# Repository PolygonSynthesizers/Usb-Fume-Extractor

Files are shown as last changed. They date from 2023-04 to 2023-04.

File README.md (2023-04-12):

# Usb-Fume-Extractor
This is a USB powered (5v) PWM Computer Fan Controller

Please read until the end!

This fume extractor is made with a 120 mm PWM (4pin) 12V PC Fan. 
You can use any 12V PC Fan as long as the power consomption doesn't exceed 500mA over 12V.
It has to be a 12V fan as the power supply is converting 5V USB to 12V. 24V Fans won't work.
I personally use a Noctua NF-F12 industrialPPC-3000 PWM and it can blow air 
along 6 meter of 80mm aluminium duct even at half speed.

You can control the speed of rotation via the potentiometer around 10 to 90% of the fan full speed.
It works with a 556 chip (which is two 555 timers in DIP 14 pins package) which produce a 5V square pulse
with pulse width modulation (it's how fan speed is controlled on a computer).

You can't power this circuit with a computer USB port. It doesn't have enough power. You have to power it with
a USB Power Supply like a Phone Charger for example. It has to be rated for 1 amp over 5V at a minimum. 
Connect the charger to the board via a USB A to USB A cable or a USB A to USB B cable (Printer cable). 
About the length : the shorter is the better.  

Some references :

* U1 is a NE556 in DIP14 package
* The inductor is a 10 uH Fastron 242408 FPS
* U2 is a LM2731 XMF in SOT-23 package
* R1 and R2 are 0805
* CF1 is 0805
* C1 is 1210
* C2 is 1812
* D1 is .5 amps Schottky Rectifier in SOD-123 package
* All through hole resistors are 1/4W
* All through hole capacitors are 5mm pitch film capacitors
* Except for C7 which is a 2mm pitch aluminium electrolytic.
* RV1 is a Alps Alpine RK09K113 10k Linear (Log can also work but control over speed will not be linear).
* SW1 is a 3 pin SPDT switch with 4.7mm pitch between pins. I has to be rated for 1A at least.

For values you can check the BOM under the bom folder. Values are also on the schematics.
All SMDs can be handsoldered. Start with the LM2731XMF.

This project has been made with KiCad 7.01. You may have to install the latest version of KiCad
for this project to work.
I have made some custom footprints for the switch, the inductor and the film capacitors.
They can be found under the Custom Footprints folder.

Gerbers are available for JLCPCB production under the Gerbers folder. 
Please make your own gerbers if you want to use an other PCB Manufacturer.

I'm providing some 3D files that can be modified on Solidworks. STL Files are also provided so you can print
them on your 3D printer. The rear body of the Fan has been made for 80mm duct. 
Feel free to modifiy it at your own conveniance.
It uses standard M4 screws for the body and M3 screws for the PCB holder.
Files can be found under the 3D Files folder. I will provide some 3d files for the base 
and the PCB front cover later. 
Don't be scared to make your own.

PLEASE DON'T TURN ON THE FAN WITHOUT THE 3D PRINTED FRONT AND REAR BODY PART ATTACHED TO IT !
IT CAN CUT OUT YOUR FINGERS VERY EASILY !
I WON'T TAKE ANY RESPONSABILITY FOR ANY DAMAGE, MATERIAL OR PHYSICAL. YOU HAVE BEEN WARNED !

ENJOY !

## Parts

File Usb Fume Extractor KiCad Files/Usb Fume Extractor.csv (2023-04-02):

# | Reference | Qty | Value | Footprint | DNP
1 | C1 | 1 | 2.2u | Capacitor_SMD:C_1210_3225Metric_Pad1.33x2.70mm_HandSolder
2 | C2 | 1 | 4.7u | Capacitor_SMD:C_1812_4532Metric_Pad1.57x3.40mm_HandSolder
3 | C3, C6 | 2 | 100nf | Capacitor_THT:C_Rect_L7.2mm_W2.5mm_P5.00mm_FKS2_FKP2_MKS2_MKP2
4 | C4 | 1 | 4.7n | Capacitor_THT:C_Rect_L7.2mm_W4.5mm_P5.00mm_FKS2_FKP2_MKS2_MKP2
5 | C5 | 1 | 10nF | Capacitor_THT:C_Rect_L7.2mm_W6.5mm_P5.00mm_FKS2_FKP2_MKS2_MKP2
6 | C7 | 1 | 2.2uF | Capacitor_THT:CP_Radial_D5.0mm_P2.00mm
7 | CF1 | 1 | 220p | Capacitor_SMD:C_0805_2012Metric_Pad1.18x1.45mm_HandSolder
8 | D1 | 1 | MBR0520 | Diode_SMD:D_SOD-123
9 | J1 | 1 | USB_B | Connector_USB:USB_B_OST_USB-B1HSxx_Horizontal
10 | J2 | 1 | Molex 2.54mm | Connector_Molex:Molex_KK-254_AE-6410-04A_1x04_P2.54mm_Vertical
11 | J3 | 1 | USB_A | Connector_USB:USB_A_Wuerth_614004134726_Horizontal
12 | JP1 | 1 | Jumper_2_Bridged | Resistor_THT:R_Axial_DIN0207_L6.3mm_D2.5mm_P10.16mm_Horizontal
13 | L1 | 1 | 10uh | Inductor_SMD:L_Fastron_242408_FPS_Handsoldering
14 | R1 | 1 | 130k | Resistor_SMD:R_0805_2012Metric_Pad1.20x1.40mm_HandSolder
15 | R2 | 1 | 15k | Resistor_SMD:R_0805_2012Metric_Pad1.20x1.40mm_HandSolder
16 | R3, R5 | 2 | 200 | Resistor_SMD:R_0805_2012Metric_Pad1.20x1.40mm_HandSolder
17 | R4 | 1 | 1K | Resistor_THT:R_Axial_DIN0207_L6.3mm_D2.5mm_P10.16mm_Horizontal
18 | R6 | 1 | 6K | Resistor_THT:R_Axial_DIN0207_L6.3mm_D2.5mm_P10.16mm_Horizontal
19 | RA1 | 1 | 6.65K | Resistor_THT:R_Axial_DIN0207_L6.3mm_D2.5mm_P10.16mm_Horizontal
20 | RA2 | 1 | 3.09K | Resistor_THT:R_Axial_DIN0207_L6.3mm_D2.5mm_P10.16mm_Horizontal
21 | RB1 | 1 | 150 | Resistor_THT:R_Axial_DIN0207_L6.3mm_D2.5mm_P10.16mm_Horizontal
22 | RV1 | 1 | 10K | Potentiometer_THT:Potentiometer_Alps_RK09K_Single_Vertical
23 | U1 | 1 | NE556 | Package_DIP:DIP-14_W7.62mm_Socket_LongPads
24 | U2 | 1 | LM2731XMF | Package_TO_SOT_SMD:SOT-23-5_HandSoldering

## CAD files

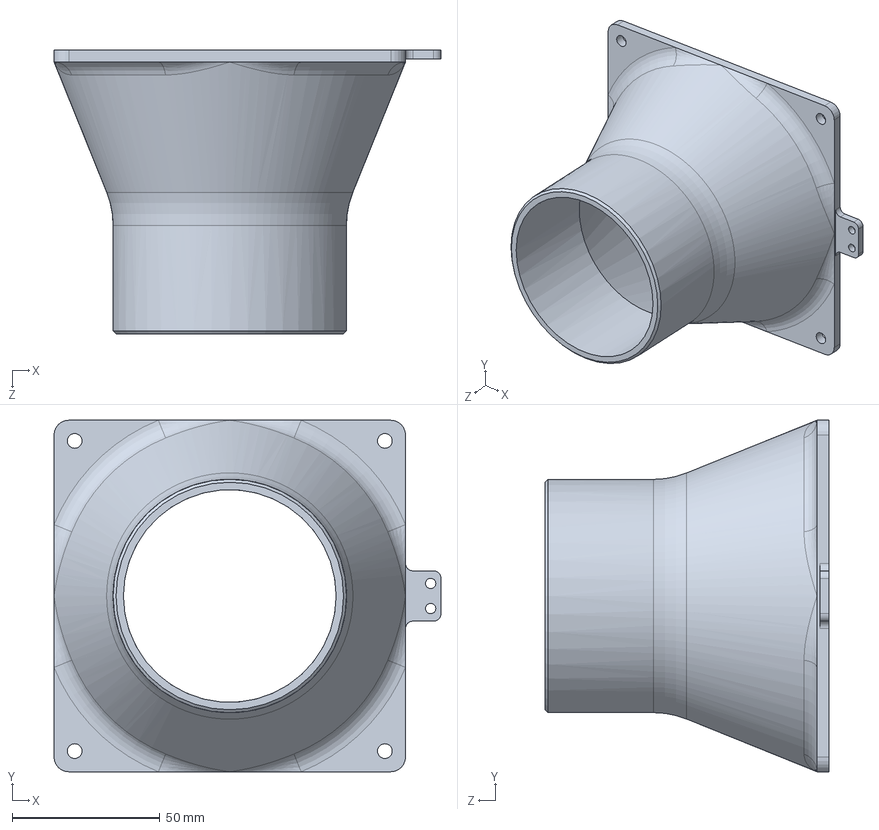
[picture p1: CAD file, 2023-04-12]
3D Files/Air_Extractor_Duct.SLDPRT
131.0 x 119.0 x 96.0 mm

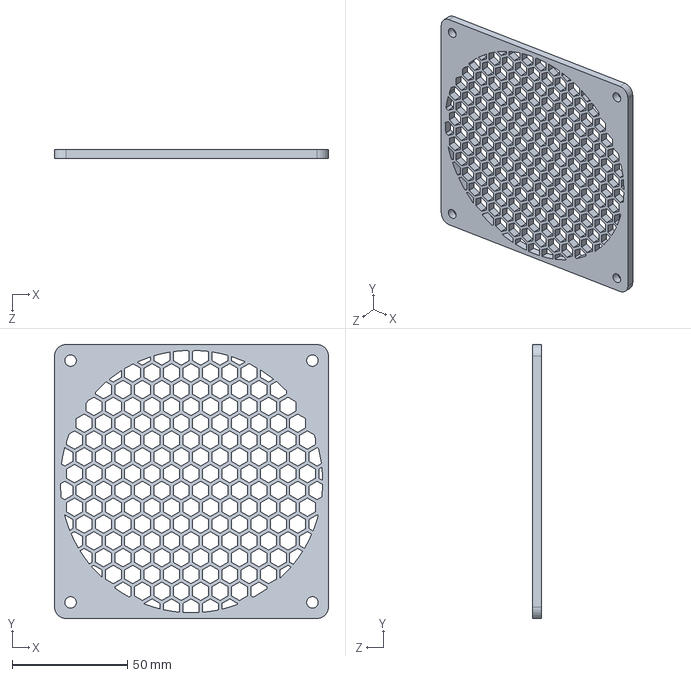
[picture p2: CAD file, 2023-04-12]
3D Files/Air_Extractor_Grid.SLDPRT
119.0 x 119.0 x 4.00 mm

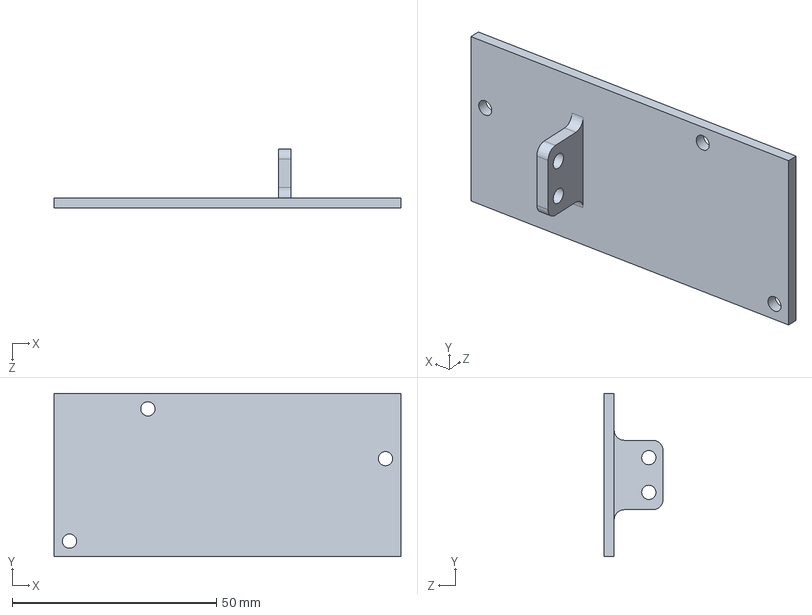
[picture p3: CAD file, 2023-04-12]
3D Files/Air_Extractor_PcbHolder_Bottom.SLDPRT
85.0 x 40.0 x 14.5 mm

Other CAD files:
3D Files/STL Files/Air_Extractor_Duct.STL
3D Files/STL Files/Air_Extractor_Grid.STL
3D Files/STL Files/Air_Extractor_PcbHolder_Bottom.STL

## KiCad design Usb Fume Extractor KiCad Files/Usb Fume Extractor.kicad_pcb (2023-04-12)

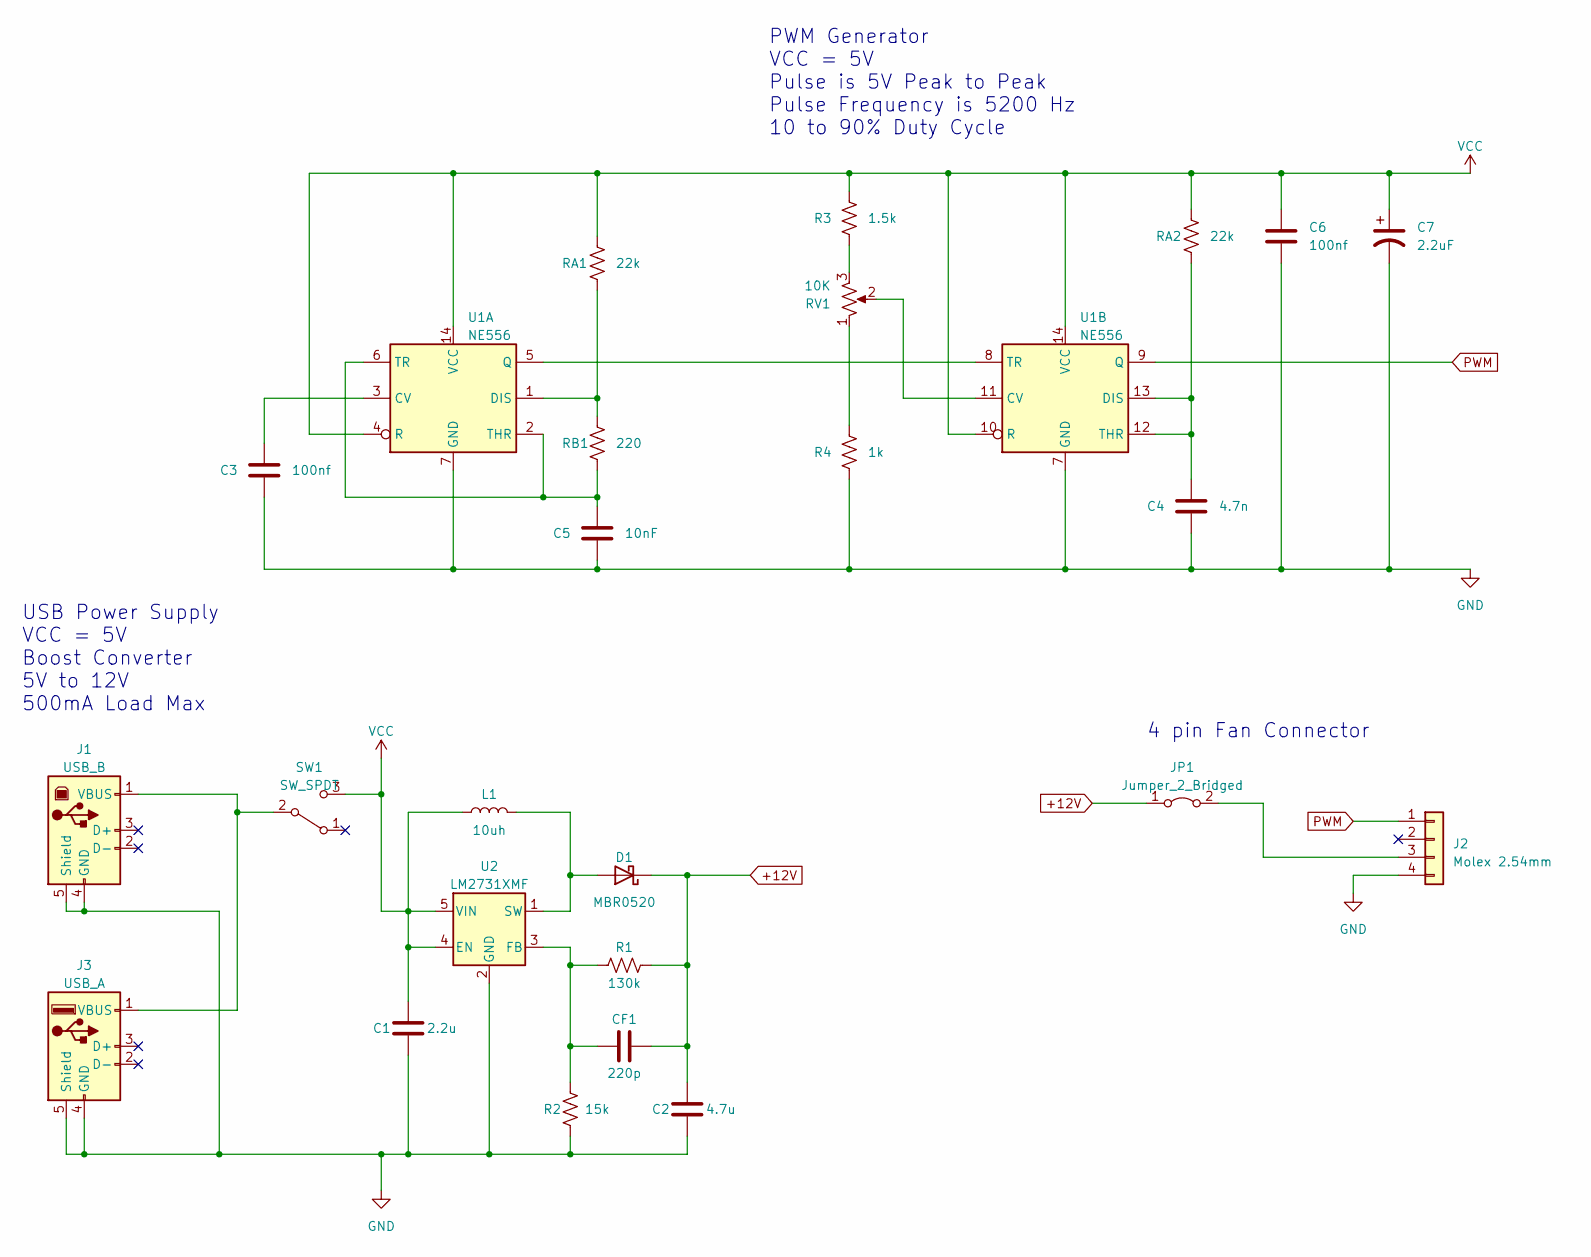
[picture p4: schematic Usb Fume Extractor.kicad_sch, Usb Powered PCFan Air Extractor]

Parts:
C1: 2.2u; C_1210_3225Metric_Pad1.33x2.70mm_HandSolder
C2: 4.7u; C_1812_4532Metric_Pad1.57x3.40mm_HandSolder
C3, C6: 100nf; C_Rect_L7.2mm_W2.5mm_P5.00mm_FKS2_FKP2_MKS2_MKP2
C4: 4.7n; C_Rect_L7.2mm_W4.5mm_P5.00mm_FKS2_FKP2_MKS2_MKP2
C5: 10nF; C_Rect_L7.2mm_W6.5mm_P5.00mm_FKS2_FKP2_MKS2_MKP2
C7: 2.2uF; CP_Radial_D5.0mm_P2.00mm
CF1: 220p; C_0805_2012Metric_Pad1.18x1.45mm_HandSolder
D1: MBR0520; D_SOD-123_Handsoldering
J1: USB_B; USB_B_OST_USB-B1HSxx_Horizontal
J2: Molex 2.54mm; Molex_KK-254_AE-6410-04A_1x04_P2.54mm_Vertical
J3: USB_A; USB_A_Wuerth_614004134726_Horizontal
JP1: Jumper_2_Bridged; R_Axial_DIN0309_L9.0mm_D3.2mm_P12.70mm_Horizontal
L1: 10uh; L_Fastron_242408_FPS_Handsoldering
R1: 130k; R_0805_2012Metric_Pad1.20x1.40mm_HandSolder
R2: 15k; R_0805_2012Metric_Pad1.20x1.40mm_HandSolder
R3: 1.5k; R_Axial_DIN0207_L6.3mm_D2.5mm_P10.16mm_Horizontal
R4: 1k; R_Axial_DIN0207_L6.3mm_D2.5mm_P10.16mm_Horizontal
RA1, RA2: 22k; R_Axial_DIN0207_L6.3mm_D2.5mm_P10.16mm_Horizontal
RB1: 220; R_Axial_DIN0207_L6.3mm_D2.5mm_P10.16mm_Horizontal
RV1: 10K; Potentiometer_Alps_RK09K_Single_Vertical
SW1: SW_SPDT; SW_DIP_SPDT_P4.7
U1: NE556; DIP-14_W7.62mm_Socket_LongPads
U2: LM2731XMF; SOT-23-5_HandSoldering

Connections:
+12V: C2.1, CF1.2, D1.1 (K), JP1.1 (A), R1.2
GND: C1.2, C2.2, C3.2, C4.2, C5.2, C6.2, C7.2, J1.4 (GND), J1.5 (Shield), J2.4, J3.4 (GND), J3.5 (Shield), R2.1, R4.2, U1.7 (GND), U2.2 (GND)
unnamed: D1.2 (A), L1.2, U2.1 (SW)
unnamed: J1.1 (VBUS), J3.1 (VBUS), SW1.2 (B)
unnamed: J2.3, JP1.2 (B)
unnamed: R3.2, RV1.3
unnamed: R4.1, RV1.1
unnamed: C3.1, U1.3 (CV)
unnamed: RA1.2, RB1.1, U1.1 (DIS)
unnamed: U1.5 (Q), U1.8 (TR)
unnamed: C5.1, RB1.2, U1.2 (THR), U1.6 (TR)
unnamed: RV1.2, U1.11 (CV)
unnamed: C4.1, RA2.2, U1.12 (THR), U1.13 (DIS)
unnamed: CF1.1, R1.1, R2.2, U2.3 (FB)
PWM: J2.1, U1.9 (Q)
VCC: C1.1, C6.1, C7.1, L1.1, R3.1, RA1.1, RA2.1, SW1.3 (C), U1.4 (R), U1.10 (R), U1.14 (VCC), U2.4 (EN), U2.5 (VIN)

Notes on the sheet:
USB Power Supply VCC = 5V Boost Converter 5V to 12V 500mA Load Max
PWM Generator VCC = 5V Pulse is 5V Peak to Peak Pulse Frequency is 5200 Hz 10 to 90% Duty Cycle
4 pin Fan Connector

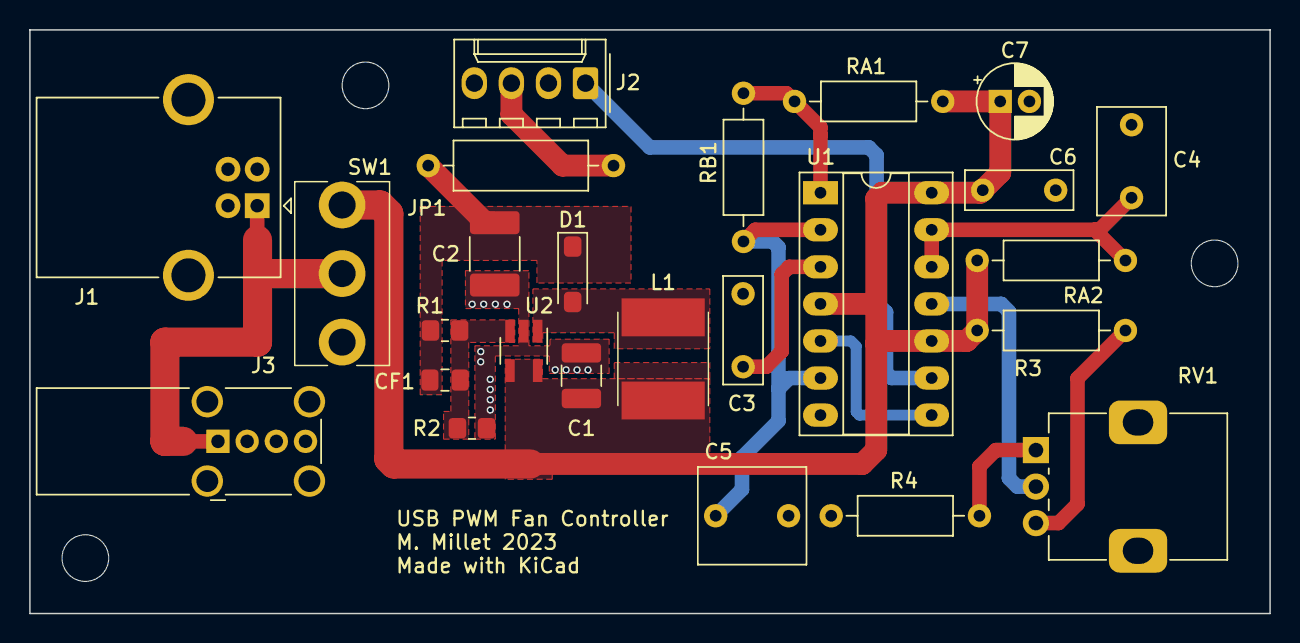
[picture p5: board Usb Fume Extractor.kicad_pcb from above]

Board: 2 copper layers, 85.0 x 40.0 mm, 25 parts (0 on the bottom side), 16 nets.
